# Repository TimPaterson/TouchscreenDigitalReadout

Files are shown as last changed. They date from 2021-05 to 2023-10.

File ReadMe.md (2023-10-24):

# Smart Touchscreen DRO for Milling Machines
__As seen in this article in [*Servo* magazine](https://www.timpaterson.com/articles/Servo/SmartDroP1_P2.pdf)!__

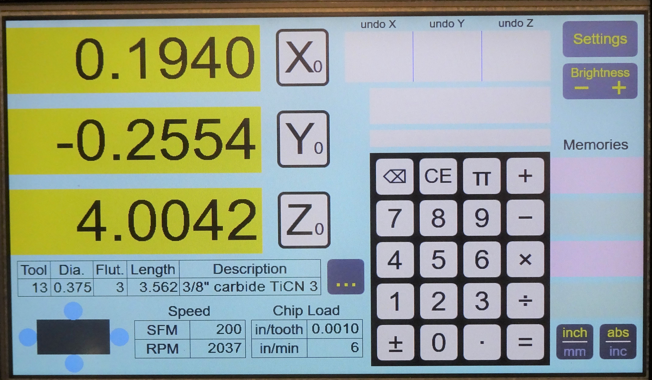
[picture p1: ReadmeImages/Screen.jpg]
Screen


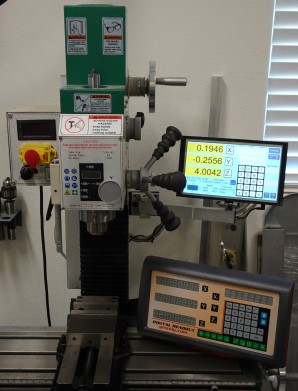
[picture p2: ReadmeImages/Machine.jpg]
Machine

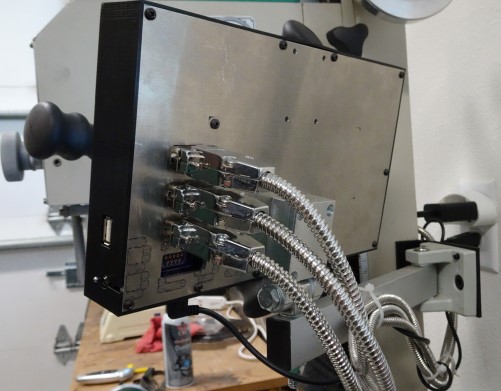
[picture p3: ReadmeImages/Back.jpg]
Back view


### Introduction
The Smart DRO is a touchscreen digital readout for milling machines. You 
can see in the photos an installation on a Grizzly mill/drill, replacing 
the original display head (shown on the mill table). The OEM position 
sensors for the X, Y, and Z axes directly connect to the back of the unit.
Position sensors like these are individually available commercially for 
mills that do not have them factory installed.

The Smart DRO can greatly simplify milling from dimensioned drawings. If 
you enter the diameter of the tool it can automatically adjust the
display reading by the tool radius. This allows you to cut at the specified 
dimension without having to add or subtract the radius offset. Note in the 
lower left corner of the main screen (the dark rectangle with a circle on 
each side): you can select which side you're cutting so it knows whether to
add or subtract the cutter radius.

You can enter the diameter of each tool as you use it, but the Smart DRO
can also keep your entire tool library (up to 500 tools) in non-volatile
memory. You can enter the list manually or import it from a flash drive
if you share it with other programs or devices. The Smart DRO will also
calculate feeds and speeds, and it displays the current feed rate when
any of the axes move.

Another helpful feature is the undo list for changes in the origin of any
axis. If you accidently zero out or set a value to the wrong axis, you can
easily recover the origin even if the axis has been moved.

The on-screen calculator allows you to include axis readings in 
calculations, and copy results back to an axis.

### Sensor Compatibility
It is industry standard that position sensors use a 9-pin "D" connector
(like a PC serial port). However, there is no standard for the pin
assignments for the connector! To solve this, the Smart DRO uses a pinout
adapter for each axis. A tiny printed circuit board with a single connector
routes signals to the correct pins. A set of 3 of these PCBs costs just 45 cents.
See the [*Servo* magazine article](https://www.timpaterson.com/articles/Servo/SmartDroP1_P2.pdf)
for more info.

### The Project
The main component is the 10" LCD touchscreen, specified in the parts 
list. This repository includes all other aspects of the hardware design 
needed to build this project as shown. These elements include:
- Custom [electronics design](https://github.com/TimPaterson/TouchscreenDigitalReadout/tree/master/Electronics),
with printed circuit board ready for fabrication.
- Enclosure design, using a 3D-printed bezel and machined aluminum back.

A [separate repository](https://github.com/TimPaterson/Touchscreen-DRO-Firmware) 
has the microcontroller firmware and graphics images.

Here are the critical links:
- The [*Servo* magazine article](https://www.timpaterson.com/articles/Servo/SmartDroP1_P2.pdf)
has complete instructions on how to build it.
- The [Touchscreen-DRO-Firmware](https://github.com/TimPaterson/Touchscreen-DRO-Firmware) repository
has firmware and everything else you need, bundled into a release.
- [Touchscreen at BuyDisplay.com](https://www.buydisplay.com/serial-spi-i2c-10-1-inch-tft-lcd-module-dislay-w-ra8876-optl-touch-panel).
Be sure to select options per the [parts list](https://github.com/TimPaterson/TouchscreenDigitalReadout/blob/master/Electronics/DroPartsList.pdf).
- [Main PCB shared at OSH Park](https://oshpark.com/shared_projects/AQX5MSFg). The
EAGLE CAD for the PCB is included is you want to use another PCB source.
- Pinout PCBs at OSH Park. Pinouts are specified by a 4-digit number where
the digits are the pin numbers on the 9-pin D-connector for GND, +5V, A, & B, respectively.
  - [2768 (Grizzly)](https://oshpark.com/shared_projects/TLEyl9I6)
  - [2134 (Jing/Jcgs)](https://oshpark.com/shared_projects/ilViDS0E)
  - [6724 (Acu-Rite)](https://oshpark.com/shared_projects/GIDBOB83)
- [Tool Library Manager](https://github.com/TimPaterson/CNC-Tool-Library-Manager)
for making tool libary files the Smart DRO can import.

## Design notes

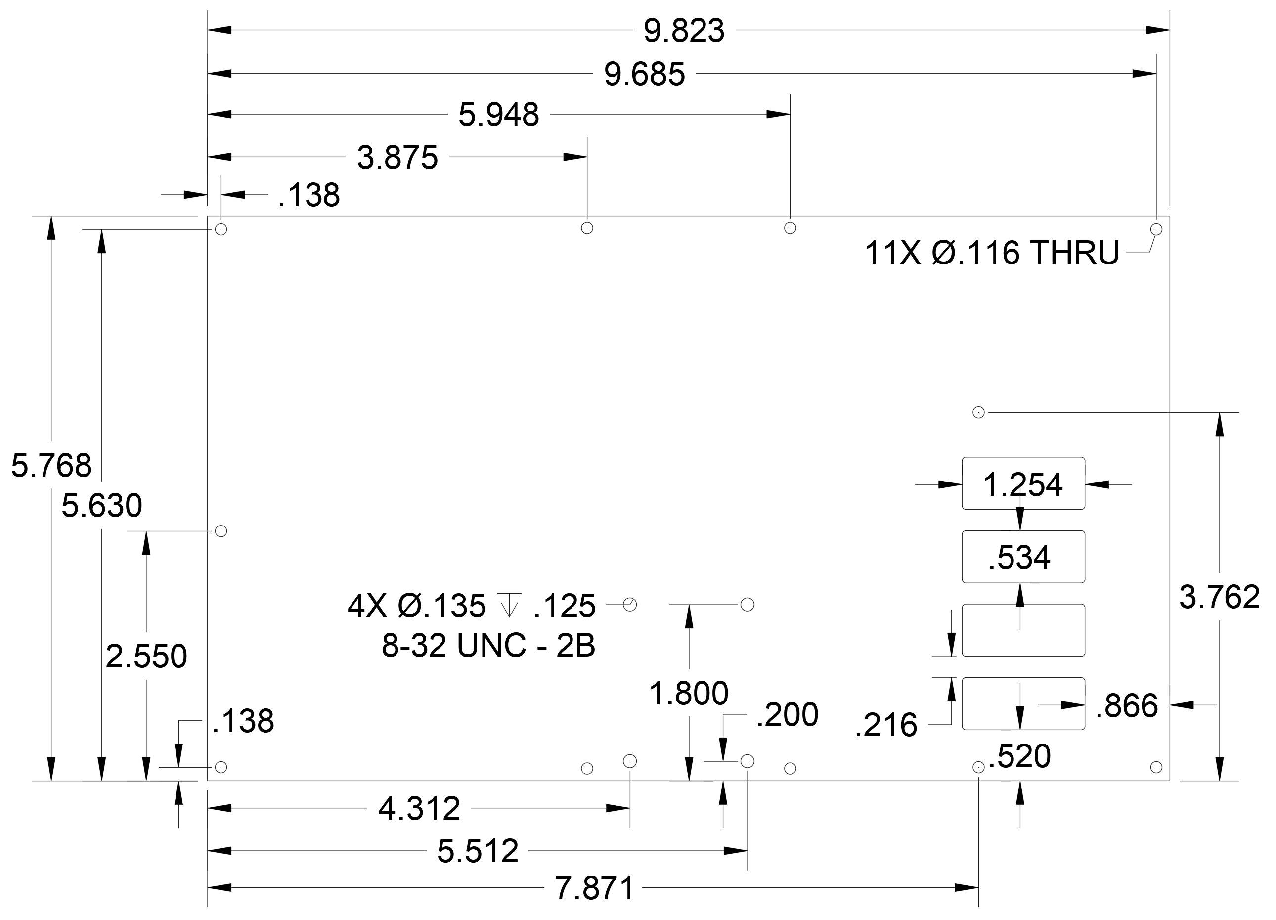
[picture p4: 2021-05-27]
Enclosure/BackPlateDrawing.png

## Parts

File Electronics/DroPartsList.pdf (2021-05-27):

Qty | Ref | Description | Package | Digi-Key Part No.
1 | C1 | 10uF capacitor | 0603
1 | C2 | 100uF capacitor | 1206 | 1276-1782-1-ND
3 | C3, C6, C15 | 1uF capacitor | 0603
7 | C4, C5, C10, C11, C12, C13, C14 | 0.1uF capacitor | 0603
1 | C7 | 4.7nF capacitor | 0603
2 | C8, C9 | 10pF capacitor | 0603
1 D1 | | MBR120VLSFT or MBR120LSFT diode | SOD123F
1 | J1 | USB micro B connector | | 609-4616-1-ND
4 | J2, J3, J4, J5 | DE-9F connector | | L77SDEH09SOL2RM8-ND
4 | J6, J7, J8, J9 | 14-pin 50-mil header | | 2057-HPH2-A-14-UA-ND
4 | J6, J7, J8, J9 | optional socket | | 609-3756-ND
1 | J10 | 4-pin 100-mil header | right angle | 1849-PR20204HBNN-ND
1 | J11 | USB-A connector | | ED2989-ND
1 | J12 | 8-pin 100-mil socket | | S7107-ND
1 | J13 | 10-pin 50-mil header | | 1175-1627-ND
1 | J14 | 40-pin 100-mil socket | | S7123-ND
1 | R1 | 33k resistor | 0603
1 | R2 | 11k resistor | 0603
1 | R3 | 1M resistor | 0603
1 | R4 | 1k resistor | 0603
1 | SW1 | toggle switch | | EG2362-ND
2 | U1, U4 | 74LCX14 logic IC | TSSOP14 | MC74LCX14DTR2GOSCT-ND
1 | U2 | MIC5504-3.3 voltage reg. | SOT23-5 | 576-4764-1-ND
1 | U3 | SAMD21J17D MCU | TQFP64 | ATSAMD21J17D-AU-ND
1 | X1 | 32.768kHz crystal | 3.2x1.5mm SMD | 2195-CM7V-T1A-32.768KHZ-7PF-10PPM-TA-QCCT-ND
4 | | 4-40 x 3/4" hex standoff | | 1772-1003-ND
3 | | 4-40 x 1/4" hex standoff | | 1772-1230-ND
1 | | 4-40 x 7/16" hex standoff | | 1772-1001-ND
11 4-40 x 1/4" screw
2 4-40 nylon insert lock nut

From BuyDisplay.com
1 ER-TFTM101-1 LCD w/options: pin header 6800 parallel; 5V; resistive touch; pin header microSD 1 Winbond W25Q128JV serial flash (install on LCD at U4)

Parts List

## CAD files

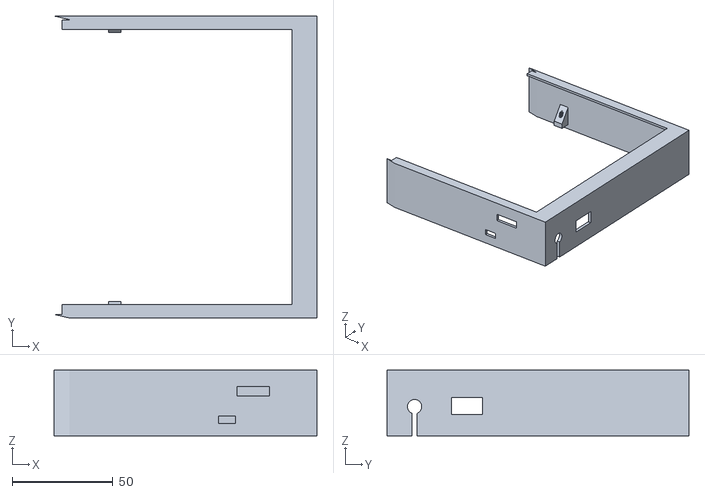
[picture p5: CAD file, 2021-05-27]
Enclosure/Right Side.stl
130.6 x 150.1 x 32.7

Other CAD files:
Enclosure/Left Side.stl

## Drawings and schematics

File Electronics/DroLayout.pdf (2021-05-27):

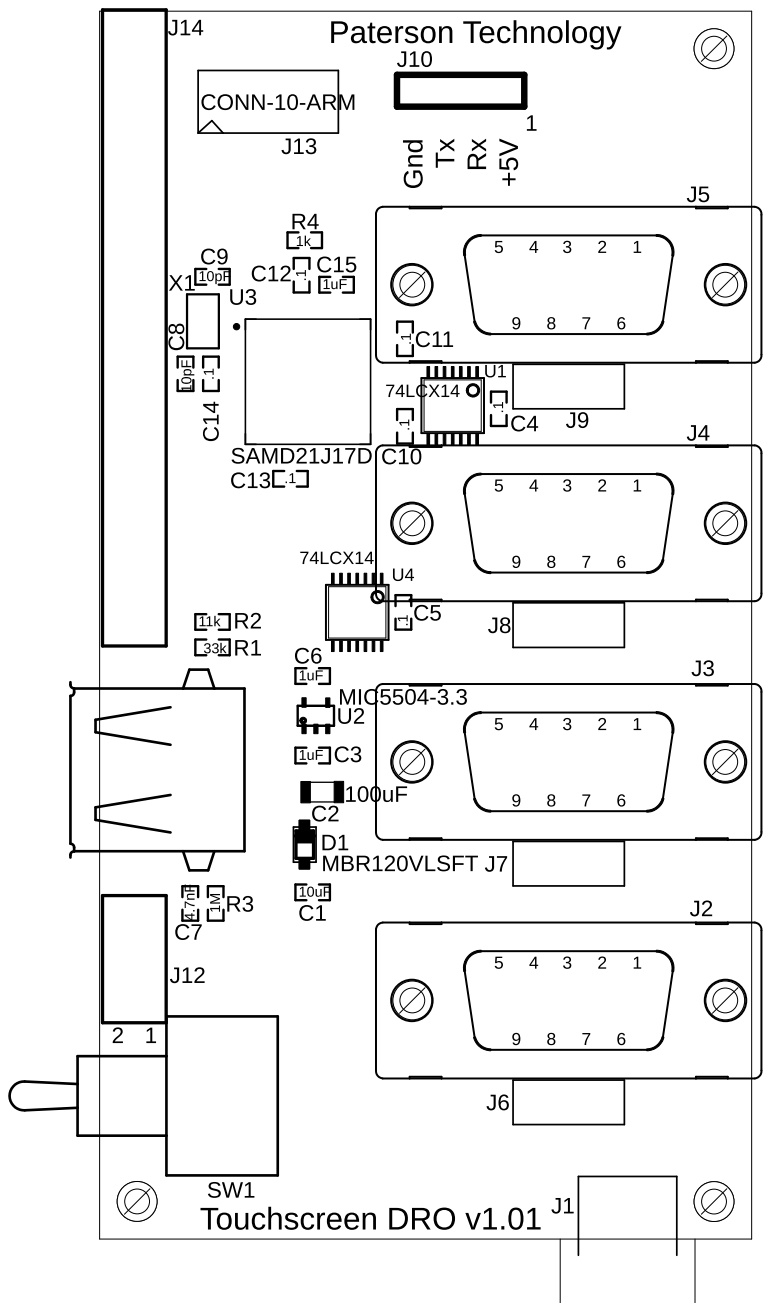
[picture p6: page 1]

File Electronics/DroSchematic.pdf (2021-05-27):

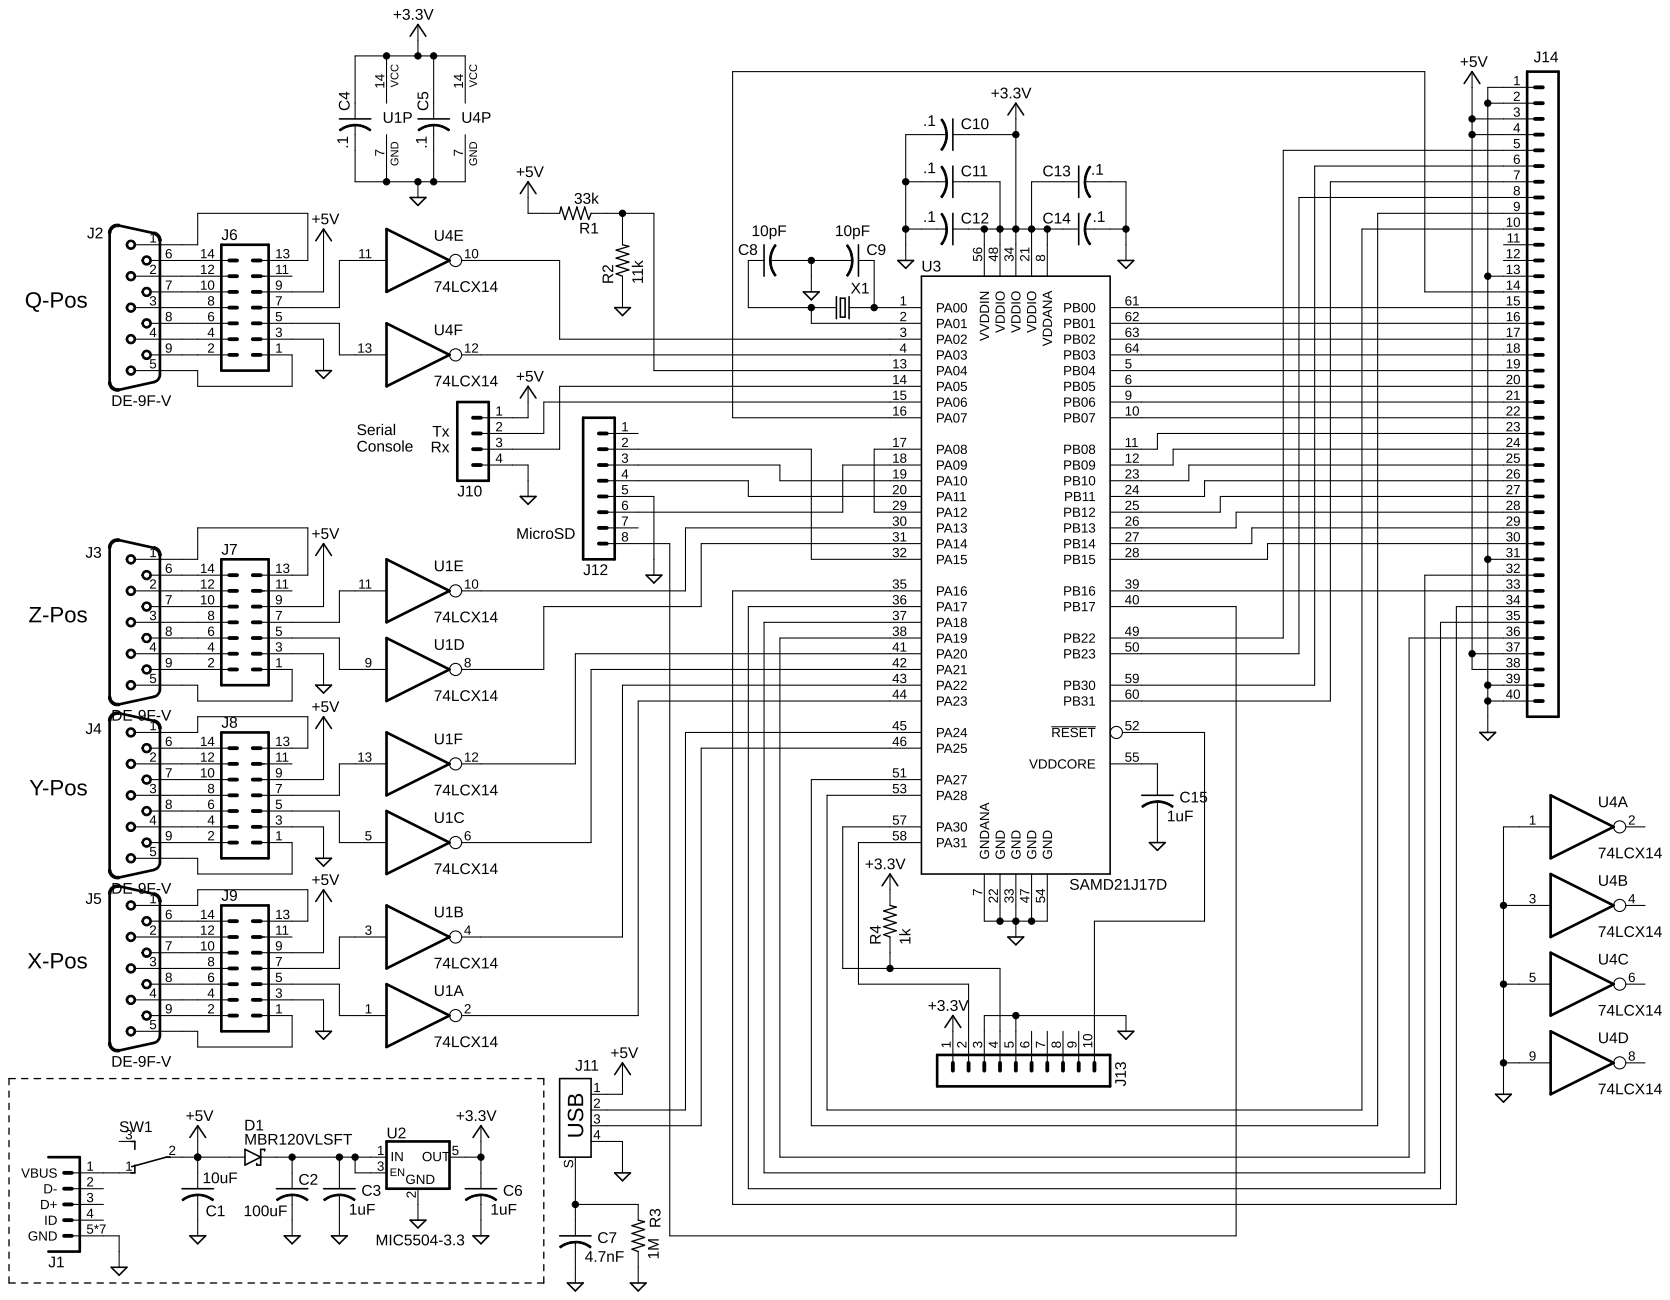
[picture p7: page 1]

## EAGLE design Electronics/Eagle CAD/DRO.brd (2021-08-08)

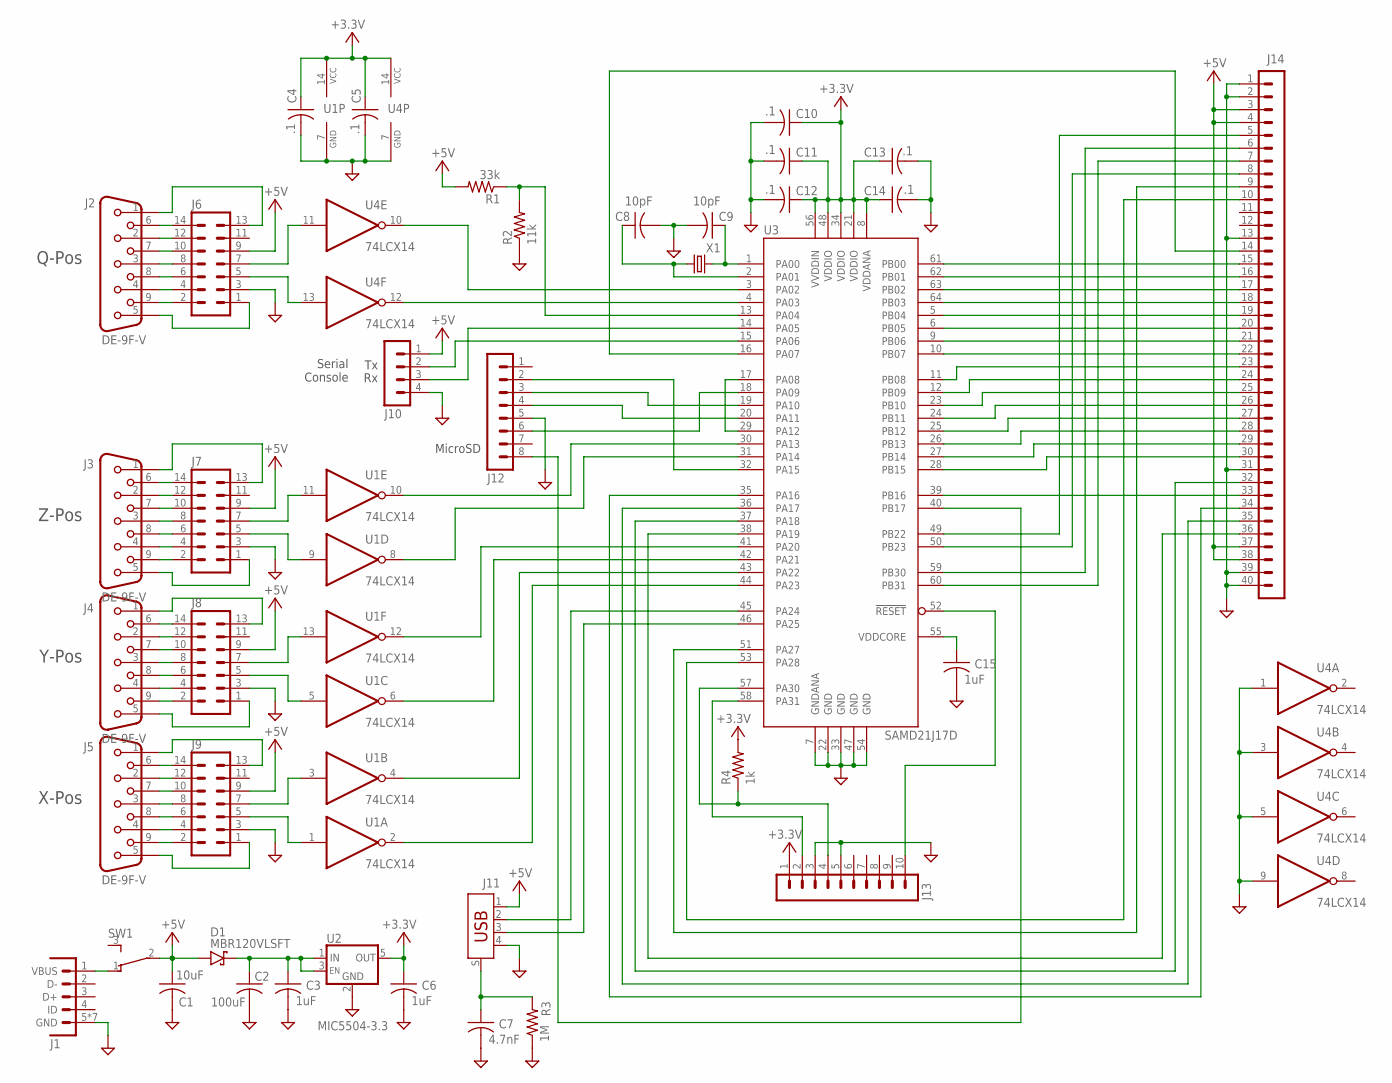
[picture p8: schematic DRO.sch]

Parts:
C1: 10uF; 0603
C2: 100uF; C1206
C3, C6, C15: 1uF; 0603
C4, C5, C10, C11, C12, C13, C14: .1; 0603
C7: 4.7nF; 0603
C8, C9: 10pF; 0603
D1: MBR120VLSFT; SOD123
J1: USB_MINI-B-MICRO-B_FCI; USB_MICRO-B_FCI
J2, J3, J4, J5: DE-9F-V; DE-9F-PCB-VERT
J6, J7, J8, J9: CONN-14-BIDI; CONN-1.27X2-14
J10: CONN-4-2.54X1-RA; CONN-2.54X1-4-RA
J11: USB-A-SHIELD; USB-A
J12: CONN-8-2.54X2; CONN-2.54X2-8
J13: CONN-10-ARM; CONN-1.27X2-10
J14: CONN-40; CONN-2.54X2-40
R1: 33k; 0603
R2: 11k; 0603
R3: 1M; 0603
R4: 1k; 0603
SW1: SWITCH-SPDT-MINI-RA-SHORT
U1, U4: 74LCX14; TSSOP14
U2: MIC5504-3.3; SOT23-5
U3: SAMD21J17D; TQFP64-0.5
X1: CRYSTAL-3X1.5; XTAL-SMD-3.2X1.5-2PIN

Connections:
+3.3V: C4.1, C5.1, C6.1, C10.1, C11.1, C12.1, C13.1, C14.1, J13.1, R4.2, U1.14 (VCC), U2.5 (OUT), U3.8 (VDDANA), U3.21 (VDDIO), U3.34 (VDDIO), U3.48 (VDDIO), U3.56 (VVDDIN), U4.14 (VCC)
+5V: C1.1, D1.A, J6.9, J7.9, J8.9, J9.9, J10.1, J11.1, J14.3, J14.4, J14.37, J14.38, R1.2, SW1.2 (C)
GND: C1.2, C2.2, C3.2, C4.2, C5.2, C6.2, C7.2, C8.2, C9.2, C10.2, C11.2, C12.2, C13.2, C14.2, C15.2, J1.5 (GND), J1.SHELL1 (GND), J1.SHELL2 (GND), J1.SHELL3 (GND), J1.SHELL4 (GND), J1.SHELL5 (GND), J1.SHELL6 (GND), J6.3, J7.3, J8.3, J9.3, J10.4, J11.4, J12.5, J13.3, J13.5, J14.1, J14.2, J14.13, J14.31, J14.39, J14.40, R2.1, R3.1, U1.7 (GND), U2.2 (GND), U3.7 (GNDANA), U3.22 (GND), U3.33 (GND), U3.47 (GND), U3.54 (GND), U4.1 (I), U4.3 (I), U4.5 (I), U4.7 (GND), U4.9 (I)
J1: J14.17, U3.63 (PB02)
unnamed: J14.15, U3.61 (PB00)
unnamed: J14.22, U3.10 (PB07)
unnamed: J14.23, U3.11 (PB08)
unnamed: J14.24, U3.12 (PB09)
unnamed: J14.25, U3.23 (PB10)
unnamed: J14.26, U3.24 (PB11)
unnamed: J14.27, U3.25 (PB12)
unnamed: J14.28, U3.26 (PB13)
unnamed: J14.29, U3.27 (PB14)
unnamed: J14.30, U3.28 (PB15)
unnamed: J14.16, U3.62 (PB01)
unnamed: J11.2, U3.45 (PA24)
unnamed: J14.18, U3.64 (PB03)
unnamed: J14.19, U3.5 (PB04)
unnamed: J14.20, U3.6 (PB05)
unnamed: J14.21, U3.9 (PB06)
unnamed: J11.3, U3.46 (PA25)
unnamed: U3.17 (PA08), U3.29 (PA12)
unnamed: R1.1, R2.2, U3.13 (PA04)
unnamed: C9.1, U3.1 (PA00), X1.2
unnamed: C8.1, U3.2 (PA01), X1.1
unnamed: C2.1, C3.1, D1.C, U2.1 (IN), U2.3 (EN)
unnamed: J13.2, U3.58 (PA31)
unnamed: C15.1, U3.55 (VDDCORE)
unnamed: J13.4, R4.1, U3.57 (PA30)
unnamed: J14.33, U3.39 (PB16)
unnamed: J13.10, U3.52 (!RESET)
unnamed: J14.5, U3.49 (PB22)
unnamed: J14.8, U3.50 (PB23)
unnamed: J14.6, U3.59 (PB30)
unnamed: J14.7, U3.60 (PB31)
unnamed: J14.10, U3.53 (PA28)
unnamed: J14.9, U3.51 (PA27)
unnamed: J14.36, U3.38 (PA19)
unnamed: J14.32, U3.37 (PA18)
unnamed: J14.35, U3.36 (PA17)
unnamed: J14.34, U3.35 (PA16)
unnamed: J12.3, U3.19 (PA10)
unnamed: J14.14, U3.16 (PA07)
unnamed: J12.6, U3.18 (PA09)
unnamed: J12.4, U3.20 (PA11)
unnamed: J12.2, U3.32 (PA15)
unnamed: U1.10 (O), U3.30 (PA13)
unnamed: J10.3, U3.14 (PA05)
unnamed: J10.2, U3.15 (PA06)
unnamed: U3.4 (PA03), U4.12 (O)
unnamed: U3.3 (PA02), U4.10 (O)
unnamed: J12.8, U3.40 (PB17)
unnamed: U1.8 (O), U3.31 (PA14)
unnamed: U1.2 (O), U3.44 (PA23)
unnamed: U1.4 (O), U3.43 (PA22)
unnamed: U1.6 (O), U3.42 (PA21)
unnamed: U1.12 (O), U3.41 (PA20)
unnamed: J6.7, U4.11 (I)
unnamed: J6.5, U4.13 (I)
unnamed: J2.5, J6.1
unnamed: J2.9, J6.2
unnamed: J2.4, J6.4
unnamed: J2.8, J6.6
unnamed: J2.3, J6.8
unnamed: J2.7, J6.10
unnamed: J2.2, J6.12
unnamed: J2.6, J6.14
unnamed: J2.1, J6.13
unnamed: J7.5, U1.9 (I)
unnamed: J8.5, U1.5 (I)
unnamed: J9.5, U1.1 (I)
unnamed: J9.7, U1.3 (I)
unnamed: J8.7, U1.13 (I)
unnamed: J7.7, U1.11 (I)
unnamed: J3.6, J7.14
unnamed: J3.2, J7.12
unnamed: J3.7, J7.10
unnamed: J3.3, J7.8
unnamed: J3.8, J7.6
unnamed: J3.4, J7.4
unnamed: J3.9, J7.2
unnamed: J4.6, J8.14
unnamed: J4.2, J8.12
unnamed: J4.7, J8.10
unnamed: J4.3, J8.8
unnamed: J4.8, J8.6
unnamed: J4.4, J8.4
unnamed: J4.9, J8.2
unnamed: J5.6, J9.14
unnamed: J5.2, J9.12
unnamed: J5.7, J9.10
unnamed: J5.3, J9.8
unnamed: J5.8, J9.6
unnamed: J5.4, J9.4
unnamed: J5.9, J9.2
unnamed: J3.1, J7.13
unnamed: J3.5, J7.1
unnamed: J4.1, J8.13
unnamed: J5.1, J9.13
unnamed: J4.5, J8.1
unnamed: J5.5, J9.1
unnamed: C7.1, J11.S (SHIELD), R3.2
VBUS: J1.1 (VBUS), SW1.1 (NC)

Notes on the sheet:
Serial Console
MicroSD
Q-Pos
Z-Pos
Y-Pos
X-Pos

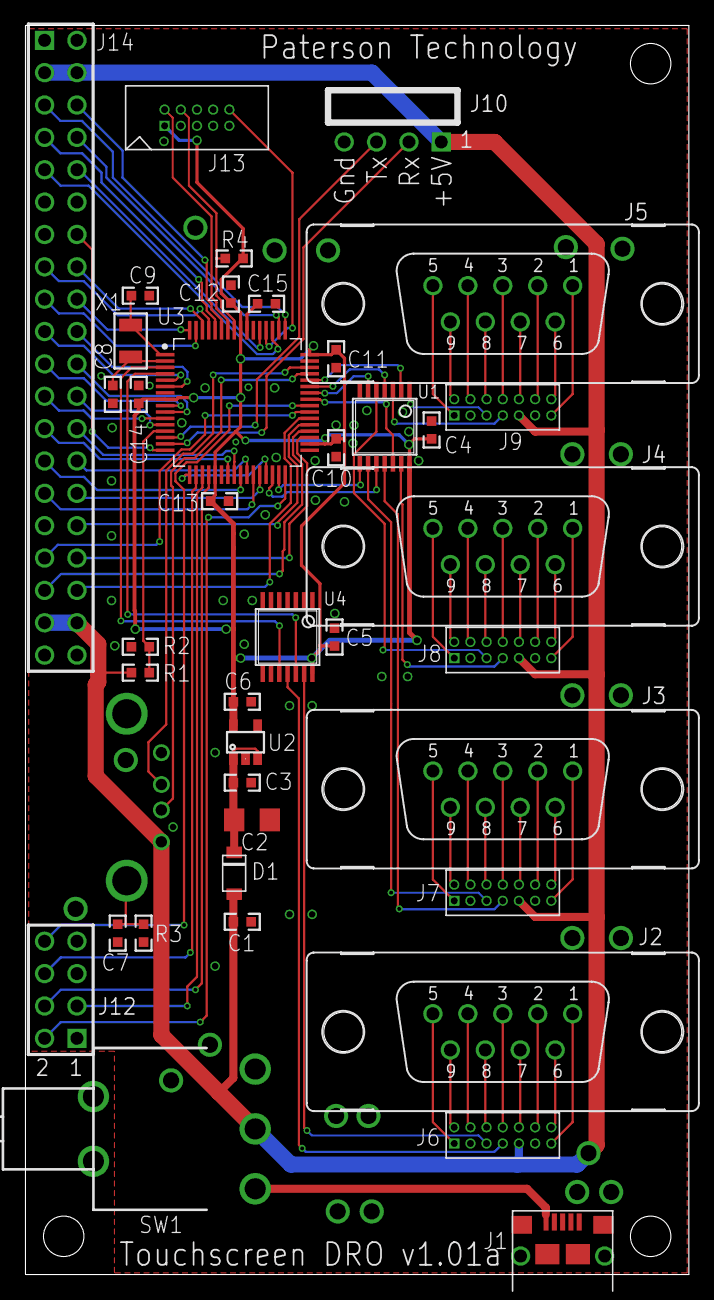
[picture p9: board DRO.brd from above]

Board: 2 copper layers, 52.1 x 98.0 mm, 40 parts (1 on the bottom side), 103 nets.

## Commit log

2020-10-15 Successfully read mill position sensor
2020-10-25 Program serial flash through SPI
2020-10-26 Use printf() to write text to LCD
2020-11-12 Add FAT file system with SD card driver, untested
2020-11-23 Add touch screen calibration, saving result to EEPROM
2020-12-17 TextField and new TextLine support printf
2020-12-23 add & implement abs/inc and inch/mm toggle buttons
2021-01-05 Automatically mount SD card or USB flash drive when present
2021-01-28 +/- key operates on current value
2021-02-19 Switch to 16-bit fonts
2021-03-07 Add touch calibration screen and rework touch calculations
2021-03-15 Display current feed rate
2021-03-18 Save axis positions & clock on power down, restore on startup
2021-03-22 Use 3-point touch calibration
2021-05-27 add all project files
    [DRO.brd, DRO.sch, Left Side.stl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]
2021-08-08 Adjust certain holes sizes in PCB designs
    [DRO.brd, DRO.sch, SensorJumper2768.brd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]
2021-11-24 Squashed 'ArmLib/' changes from 1744b72..6003bf1
    6003bf1 Add support for SAM 3/SAM 4
    90fe42b Improve accuracy of ShortDelay() in TimerLib
    1a0828c resolve interference between SetPortMux() and SetPortConfig()
    e68fe99 Make interrupts optional for DMA
    git-subtree-dir: ArmLib
    git-subtree-split: 6003bf13b35d386b4e0ccba8bcb133a540c0b381
2023-10-24 Firmware split into separate repository
    [Left Side.stl, Right Side.stl]
